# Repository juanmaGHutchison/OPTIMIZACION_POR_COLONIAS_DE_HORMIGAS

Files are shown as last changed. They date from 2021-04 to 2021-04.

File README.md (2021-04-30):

# Proyecto Final de Carrera: Diseño y Fabricación de Robots basados en Arduino para realizar el Algoritmo de Colonias de Hormigas.

_El proyecto permite realizar una ejecución real del Algoritmo de Colonias de Hormigas en un robot diseñado y fabricado en Arduino, diseño del robot disponible en el mismo proyecto._

Podemos encontrar una breve explicación además de una ejecución del robot finalizado en el siguiente enlace:
* [Ejecución ACO en Arduino](https://www.youtube.com/watch?v=iJVlAWncoFY&t=352s) - Video explicativo con posterior ejecución del Algoritmo de Colonias de Hormigas.

Y tenemos otro video en el cual se detalla el montaje de dicho robot en Arduino:
* [Montaje robot ACO](https://www.youtube.com/watch?v=88lnHN8jg98) - Video explicativo del montaje del robot en Arduino.

## Descripcion de directorios y archivos

_Descripción de los directorios y archivos disponibles en el proyecto:_

* 'ACO_CPP': En este directorio se encuentran los archivos necesarios para ejecutar el Algoritmo de Colonias de Hormigas en el lenguaje C++. De este programa se ha realizado gran parte de la experimentación del archivo 'Gomez-Hutchison-JuanManuel_TFG' Capítulo 4.
* 'ACOv2_robot': En este directorio se encuentra el proyecto final realizado en Arduino el cual se cargará físicamente al Robot.
* 'ACOv2_servidor': En este directorio se encuentra la parte del servidor, el cual se encargará, entre otras funciones de comunicar a las hormigas y actualizar las feromonas del mapa.
* 'BLUETOOTH_PRUEBA': En este directorio se encuentra un código simple para testear la comunicación Bluetooth entre el Robot y el servidor.
* 'CNYboardV2.0': Directorio donde se almacena el proyecto de diseño de la PCB al que irán conectados los sensores CNY70. Podemos encontrar la información en la documentación del archivo 'Gomez-Hutchison-JuanManuel_TFG', Sección 3.3.4.1.
* 'TEST_PIEZAS_HORMIGAS': Directorio que contiene código en Arduino para el testeo de piezas individuales del Robot, sensores, actuadores... así como de algunas pruebas de integración de éstos. 
* 'shieldV2.0.1': Directorio donde se almacena el proyecto de diseño de la PCB al que irán interconectados todos los componentes electrónicos. Podemos encontrar la información en la documentación del archivo 'Gomez-Hutchison-JuanManuel_TFG', Sección 3.3.4.2.
* 'Diseño_soporte3D': Directorio que contiene el diseño del soporte de la batería de nuestro robot.
* 'Mapa': Directorior que contiene el diseño del mapa así como las imágenes listas para imprimir.
* 'Gomez-Hutchison-JuanManuel_TFG': Archivo que contiene la documentación completa del proyecto, para cualquier tipo de duda referente al proyecto, acceder a este archivo.

### Pre-requisitos 

_Que cosas necesitas para instalar el software:_

* Arduino IDE en su última versión.
* Qt creator v4.4.10 o superior.
* Opcional: Compilador clang++ para ejecución del código en C++. Compilado con Makefile.

### Instalación 

_Simplemente tendremos que cargar el código en Arduino en el robot una vez fabricado, imprimir el mapa sobre el que se lanzará al Robot, y en un PC el código del servidor creado en Qt._

## Ejecutando las pruebas 

_Para la obtención de resultados iniciamos el servidor en Qt, lanzamos el Robot en el mapa y seguimos los pasos descritos en el documento 'Gomez-Hutchison-Juanmanuel_TFG' en la Sección 3.10_

### Analice las pruebas end-to-end 

_Los resultados de las pruebas realizadas y contrastadas a la vez que justificadas las encontramos en el documento 'Gomez-Hutchison-Juanmanuel_TFG' en el Capítulo 4_

## Construido con 

_Herramientas utilizadas para el proyecto_

* [Qt creator](https://www.qt.io/product/development-tools) - Usado para hacer el programa servidor.
* [Arduino IDE](https://www.arduino.cc/) - Usado para hacer el programa del Robot en Arduino 
* [Clang](https://clang.llvm.org/) - Usado para compilar el Programa en C++
* [GnuPlot](http://www.gnuplot.info/) - Usado para generar Gráficas
* [Eagle](https://www.autodesk.com/products/eagle/overview?plc=F360&term=1-YEAR&support=ADVANCED&quantity=1) - Usado para realizar el diseño de las PCB
* [Fusion 360](https://www.autodesk.es/products/fusion-360/overview?term=1-YEAR) - Usado para realizar el diseño 3D
* [InkScape](https://inkscape.org/es/) - Usado para el diseño del mapa
* [Latex](https://es.overleaf.com) - Usado para escribir la documentación.

## Autores 

_Ayudas ofrecidas_

* **Arturo Morgado Estévez** - *Estructuración del proyecto y electrónica*
* **Abel García Otero** - *Electrónica*
* **Ignacio Díaz Cano** - *Documentación y codificación* - [ignaciodc](https://github.com/ignaciodc)

---
Realizado por [juanmaGHutchison](https://github.com/juanmaGHutchison)

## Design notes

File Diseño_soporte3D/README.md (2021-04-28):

# Diseño del soporte 3D para la batería.

_Estructura de soporte para batería la cuál va atornillada a la parte inferior del chasis del robot._

## Descripción de archivos del directorio

_Descripción de los archivos principales de este directorio:_

* 'soporte.stl': archivo stl para futura impresión 3D.

### Pre-requisitos 

_Programa propio de la impresora para imprimir el archivo_

## Construido con 

_Herramientas utilizadas para el proyecto_

* [Fusion 360](https://www.autodesk.es/products/fusion-360/overview?term=1-YEAR) - Usado para realizar el diseño 3D

---
Realizado por [juanmaGHutchison](https://github.com/juanmaGHutchison)

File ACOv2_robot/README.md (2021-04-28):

# Algoritmo de Colonias de Hormigas: Robot en Arduino.

_Código en Arduino(C++) que simula como la hormiga busca comida, se toma parte del Algoritmo de colonias de hormigas, la decisi n de tomar el camino._

## Descripci n de archivos del directorio

_Descripción del archivo principal de este directorio. El resto de archivos podemos encontrarlos descritos en el documento 'Gomez-Hutchison-JuanManuel_TFG' en la Sección 3.5.2:_

* 'ACOv2_robot.ino': Código principal en Arduino, el cual cargaremos en el robot físicamente.

### Pre-requisitos 

_Que cosas necesitas para instalar el software:_

* Arduino IDE en su  ltima versi n.

### Instalación 

_Cargamos el código en el puerto serie al que está conectado el robot al PC._

## Ejecutando las pruebas 

_Para la ejecuci n debemos arrancar el servidor, posicionar sobre el nodo azul del mapa al robot, encenderlo, y pulsar sobre el botón 'Init pheromones' en el programa servidor._

## Construido con 

_Herramientas utilizadas para el proyecto_

* [Arduino IDE](https://www.arduino.cc/) - Usado para hacer el programa del Robot en Arduino 

---
Realizado por [juanmaGHutchison](https://github.com/juanmaGHutchison)

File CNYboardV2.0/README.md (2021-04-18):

# Diseño de Circuito Impreso para sensores CNY70.

_Proyecto realizado en Eagle donde se muestran los esquemáticos y el diseño de dicho esquemático donde se interconectan los sensores ópticos infrarrojos CNY70._

## Descripción de archivos del directorio

_Descripción de los archivos principales de este directorio:_

* 'CNYboard.brd': Diseño del circuito impreso.
* 'CNYboard.pdf': PDF donde se muestra el diseño realizado en el archivo 'CNYboard.brd'.
* 'CNYboard.sch': Esquemático del circuito impreso.
* 'CNYboard.pdf': PDF donde se muestra el esquemático realizado en el archivo 'CNYboard.sch'.
* 'eagle.epf': Archivo de tipo proyecto, el cual abrira los archivos en el programa Eagle.

### Pre-requisitos 

_Que cosas necesitas para instalar el software:_

* Autodesk Eagle en su última versión.

## Ejecutando las pruebas 

_PCB totalmente testeada tanto por software con la herramienta DRC, tanto impresa, de manera empírica._

## Construido con 

_Herramientas utilizadas para el proyecto_

* [Eagle](https://www.autodesk.com/products/eagle/overview?plc=F360&term=1-YEAR&support=ADVANCED&quantity=1) - Usado para realizar el diseño de las PCB

---
Realizado por [juanmaGHutchison](https://github.com/juanmaGHutchison)

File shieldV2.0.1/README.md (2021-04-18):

# Diseño de Circuito Impreso para la interconexión de componentes.

_Proyecto realizado en Eagle donde se muestran los esquemáticos y el diseño de dicho esquemático donde se interconectan los componentes electrónicos._

## Descripción de archivos del directorio

_Descripción de los archivos principales de este directorio:_

* 'shield.brd': Diseño del circuito impreso.
* 'shield.pdf': PDF donde se muestra el diseño realizado en el archivo 'shield.brd'.
* 'shield.sch': Esquemático del circuito impreso.
* 'shield.pdf': PDF donde se muestra el esquemático realizado en el archivo 'shield.sch'.
* 'eagle.epf': Archivo de tipo proyecto, el cual abrira los archivos en el programa Eagle.

### Pre-requisitos 

_Que cosas necesitas para instalar el software:_

* Autodesk Eagle en su última versión.

## Ejecutando las pruebas 

_PCB totalmente testeada tanto por software con la herramienta DRC, tanto impresa, de manera empírica._

## Construido con 

_Herramientas utilizadas para el proyecto_

* [Eagle](https://www.autodesk.com/products/eagle/overview?plc=F360&term=1-YEAR&support=ADVANCED&quantity=1) - Usado para realizar el diseño de las PCB

---
Realizado por [juanmaGHutchison](https://github.com/juanmaGHutchison)

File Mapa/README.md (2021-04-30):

# Diseño del mapa sobre el que se ejecutará el robot.

_Mapa que representa el grafo sobre el que el robot en Arduino realizará la ejecución. Se imprimirá dicho diseño en papel Din A3._

## Descripción de archivos del directorio

_Descripción de los archivos principales de este directorio:_

* 'mapaV4.svg': archivo para editar el mapa.
* 'mapaV4.png': foto del archivo del mapa.
* 'mapaV4.pdf': archivo pdf que contiene la foto del mapa, perfecto para imprimir.

## Construido con 

_Herramientas utilizadas para el proyecto_

* [InkScape](https://inkscape.org/es/) - Usado para el diseño del mapa

---
Realizado por [juanmaGHutchison](https://github.com/juanmaGHutchison)

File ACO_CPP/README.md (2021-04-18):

# Algoritmo de Colonias de Hormigas en C++.

_Código en C++ para la ejecución completa del Algoritmo de Colonias de Hormigas, este código es independiente del robot, se puede ejecutar para la comprobación de resultados._

## Descripción de archivos del directorio

_Descripción de los archivos disponibles en este directorio:_

* 'camino.hpp': Contiene todo lo referente a los caminos que tome la hormiga así como de crear el mapa (Grafo).
* 'hormigas.hpp': Contiene las operaciones y atributos que definen una hormiga.
* 'listaenla.hpp': Se utiliza el ##Tipo Abstracto de Datos## Lista con la implementación de nodos enlazados para guardar el recorrido que ha tomado una hormiga para así derivar posteriormente, su costo.
* 'Makefile': Script para compilar el código descrito en este directorio ejecutando el comando 'make' se generará automáticamente el archivo ejecutable. Se utiliza el compilador 'Clang++'.
* 'pt.cpp': La iniciales del archivo 'pt' significan 'prueba tablero', hace referencia al código principal de ejecución.
* 'tablero.hpp': Este archivo es el más importante ya que enlaza casi todas las clases implementadas con la principal 'pt.cpp'.

Todo lo mencionado en este apartado lo podemos encontrar en la Sección 3.2.3.

### Pre-requisitos 

_Que cosas necesitas para instalar el software:_

* Compilador clang++ para ejecución del código en C++. 
* Ejecutar el archivo 'Makefile' sobre una terminal Linux.

### Instalación 

_Posicionado con una terminal en Linux sobre este directorio ejecutamos el comando:_

```
make
```

## Ejecutando las pruebas 

_Para la ejecución del código en C++ después de completar la ##Instalación## se generará el archivo 'test-tablero' el cual será ejecutable_

```
./test-tablero
```

## Construido con 

_Herramientas utilizadas para el proyecto_

* [Clang](https://clang.llvm.org/) - Usado para compilar el Programa en C++

---
Realizado por [juanmaGHutchison](https://github.com/juanmaGHutchison)

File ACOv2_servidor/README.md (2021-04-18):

# Algoritmo de Colonias de Hormigas: Servidor del robot.

_Código en C++ referente al servidor realizado en Qt._

## Descripción de archivos del directorio

_Descripción de los archivos del proyecto servidor disponibles en el documento 'Gomez-Hutchison-JuanManuel_TFG' en la Sección 3.8.3._

### Pre-requisitos 

_Que cosas necesitas para instalar el software:_

* QtCreator v4.4.10 o superior.

### Instalación 

_Cargar el programa en el IDE del QtCreator y generar un archivo ejecutable o bien ejecutarlo desde el mismo IDE._

## Ejecutando las pruebas 

_Para la ejecución debemos arrancar el servidor, posicionar sobre el nodo azul del mapa al robot, encenderlo, y pulsar sobre el botón 'Init pheromones' en el programa servidor­._

## Construido con 

_Herramientas utilizadas para el proyecto_

* [Qt creator](https://www.qt.io/product/development-tools) - Usado para hacer el programa servidor.

---
Realizado por [juanmaGHutchison](https://github.com/juanmaGHutchison)

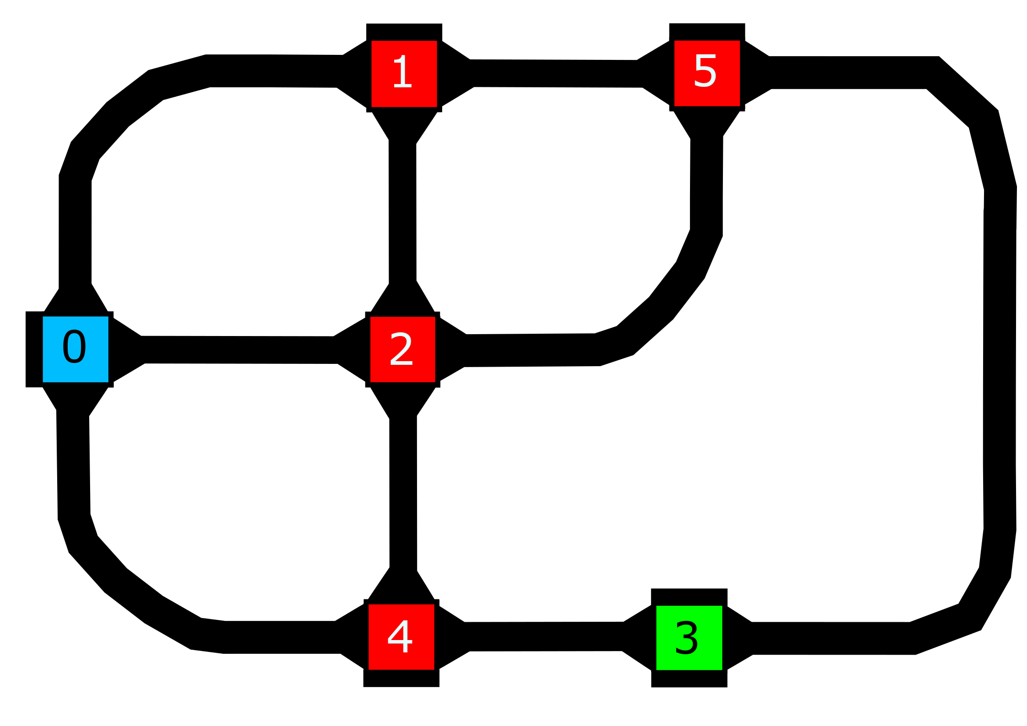
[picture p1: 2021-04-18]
ACOv2_servidor/pictures/mapa-Picture.png

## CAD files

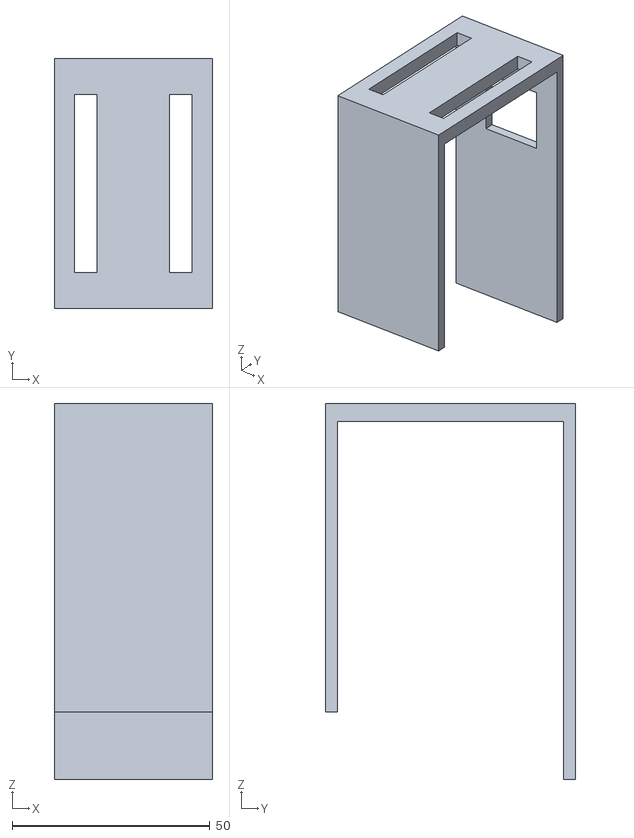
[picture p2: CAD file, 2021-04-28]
Diseño_soporte3D/soporte.stl
40.0 x 63.3 x 95.0

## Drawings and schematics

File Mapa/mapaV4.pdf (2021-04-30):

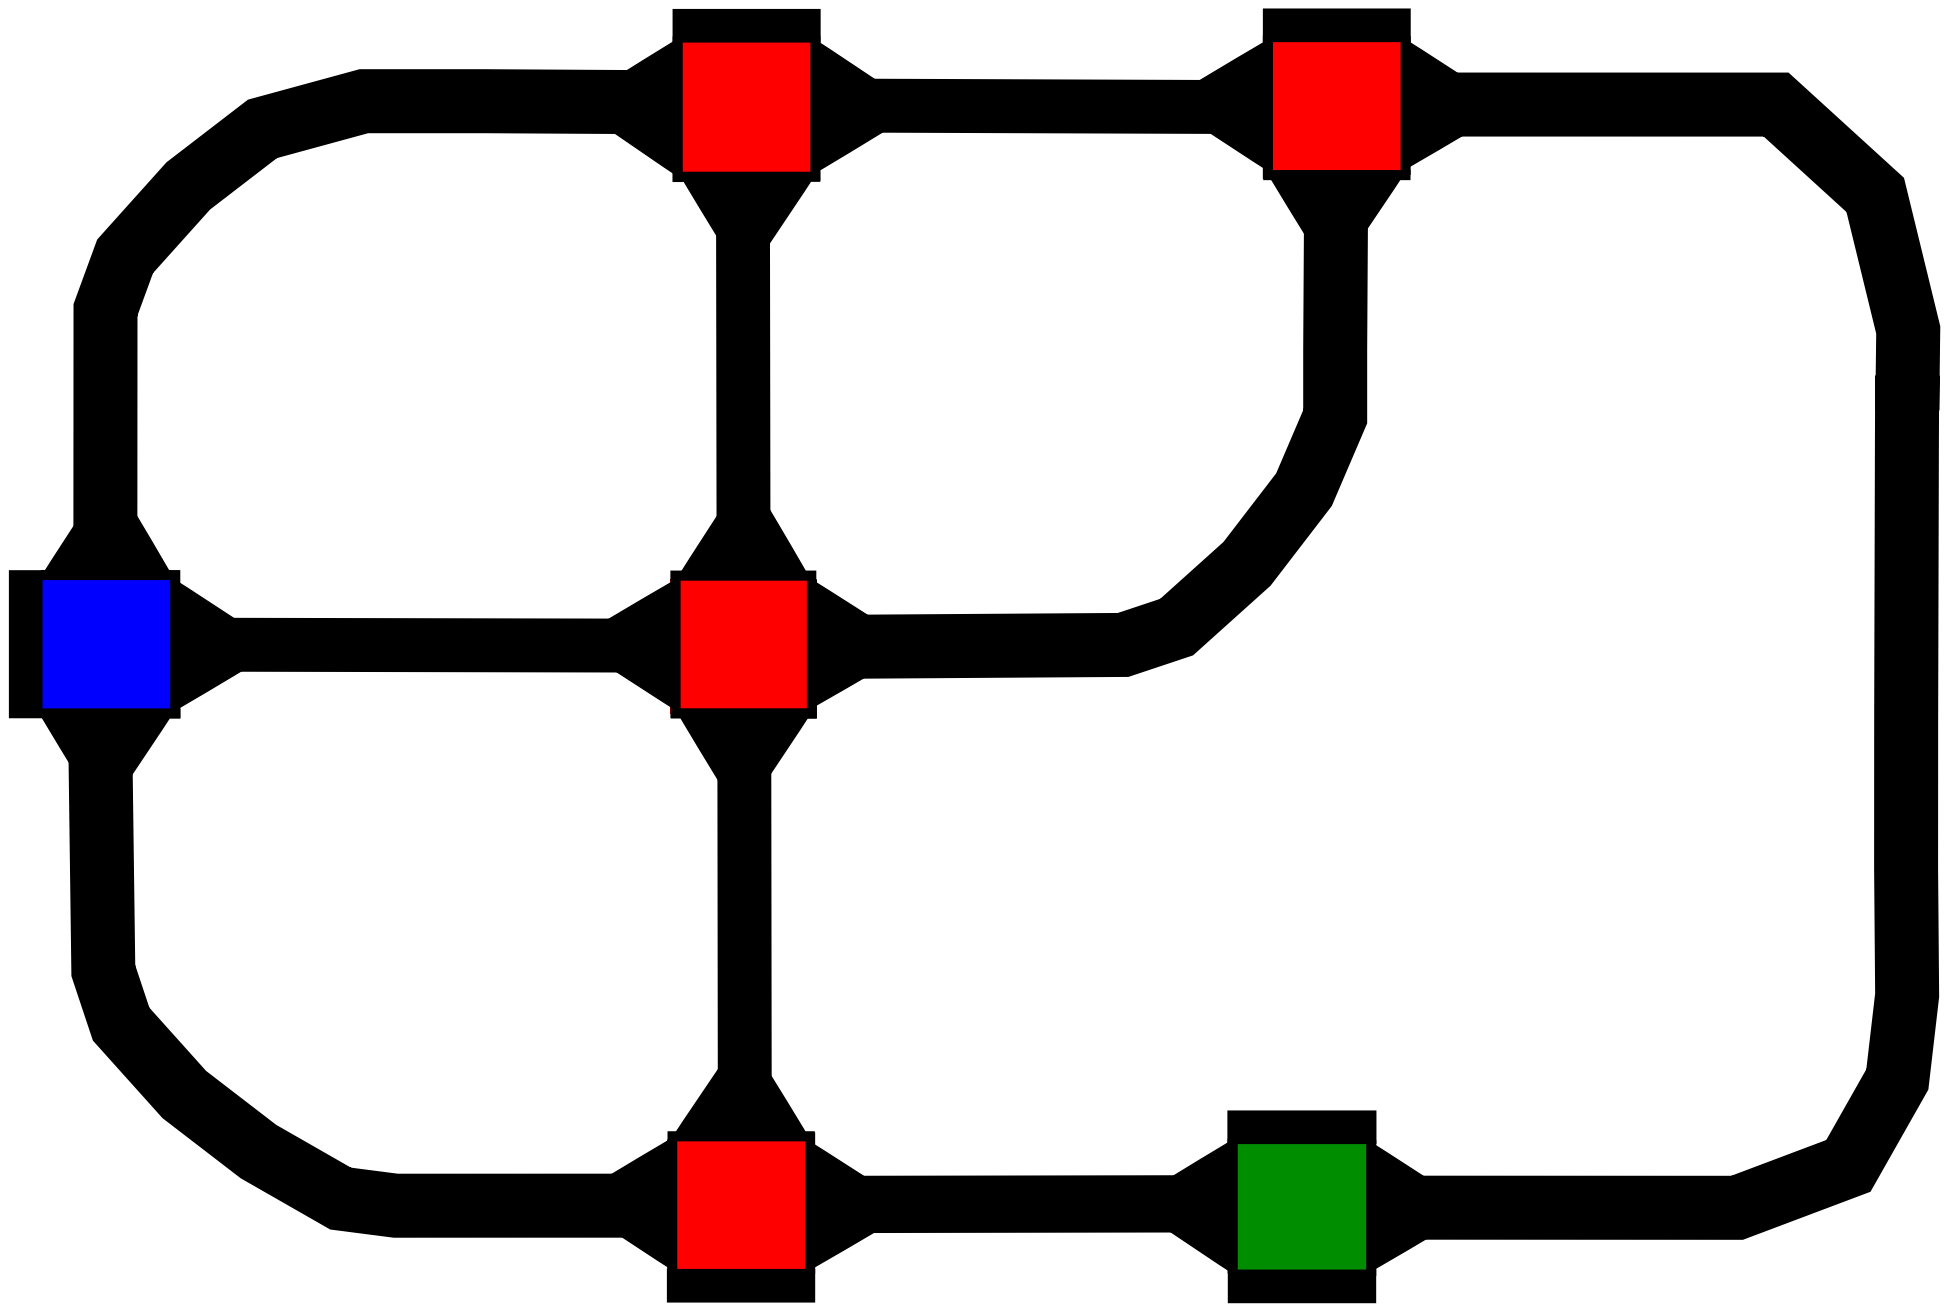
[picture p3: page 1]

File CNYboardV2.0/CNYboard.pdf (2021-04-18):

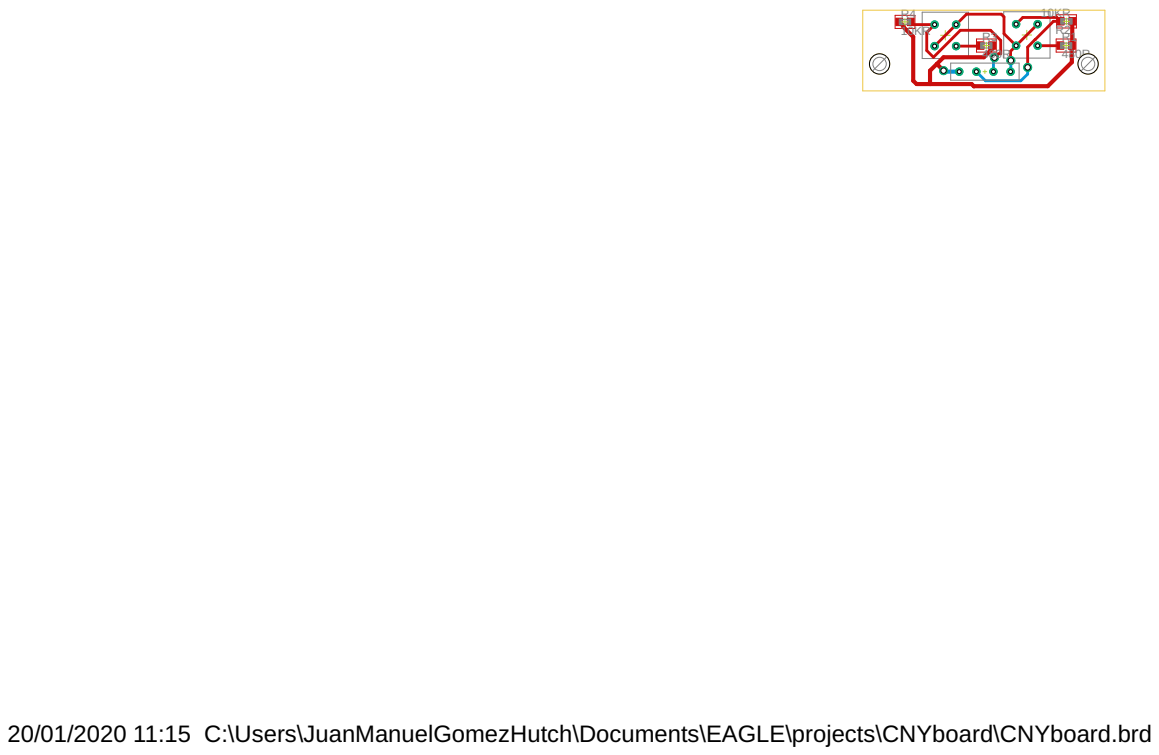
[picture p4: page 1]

20/01/2020 11:15 C:\Users\JuanManuelGomezHutch\Documents\EAGLE\projects\CNYboard\CNYboard.brd

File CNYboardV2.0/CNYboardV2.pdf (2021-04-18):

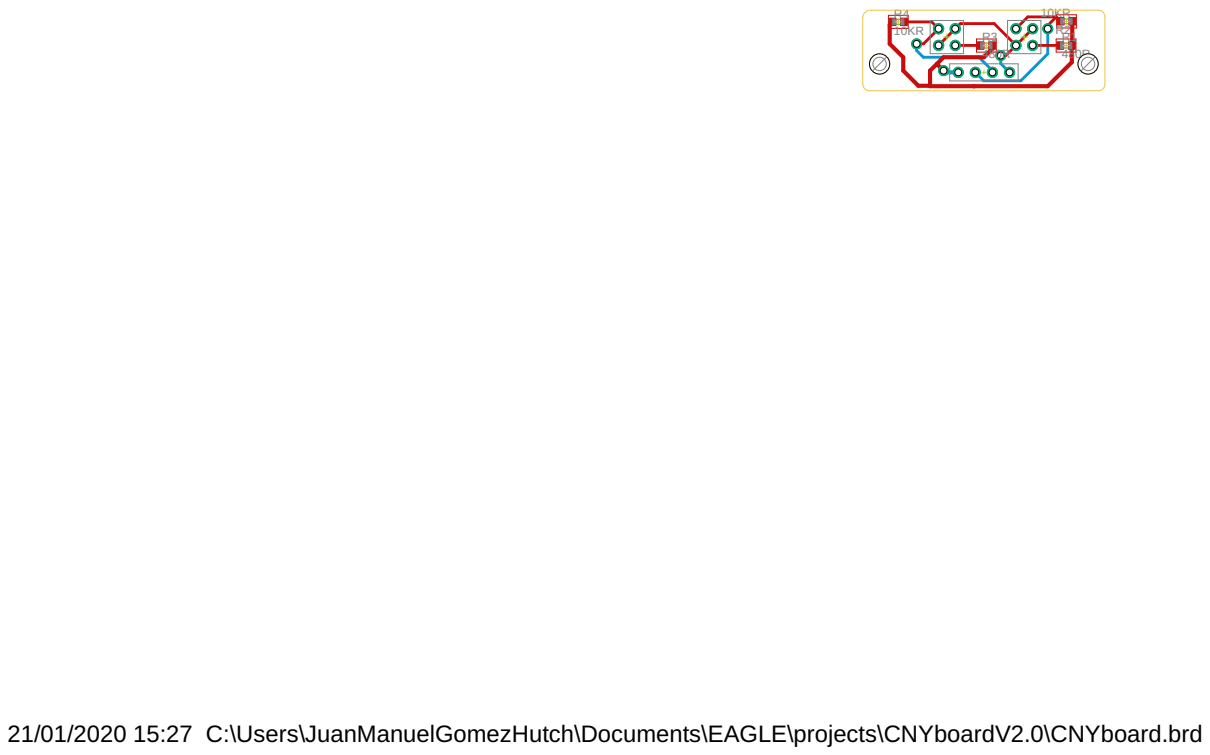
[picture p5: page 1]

21/01/2020 15:27 C:\Users\JuanManuelGomezHutch\Documents\EAGLE\projects\CNYboardV2.0\CNYboard.brd

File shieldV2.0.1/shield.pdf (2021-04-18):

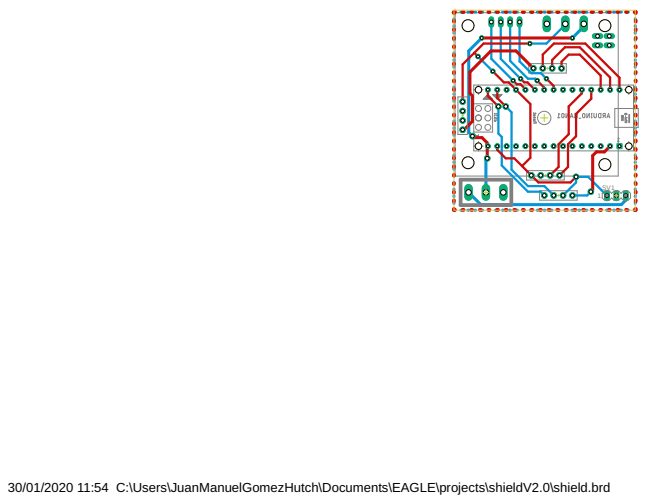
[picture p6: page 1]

30/01/2020 11:54 C:\Users\JuanManuelGomezHutch\Documents\EAGLE\projects\shieldV2.0\shield.brd

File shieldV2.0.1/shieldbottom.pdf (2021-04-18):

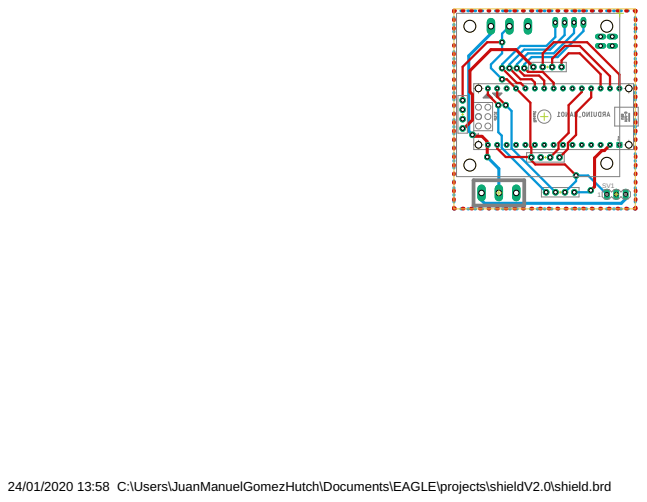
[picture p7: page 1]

24/01/2020 13:58 C:\Users\JuanManuelGomezHutch\Documents\EAGLE\projects\shieldV2.0\shield.brd

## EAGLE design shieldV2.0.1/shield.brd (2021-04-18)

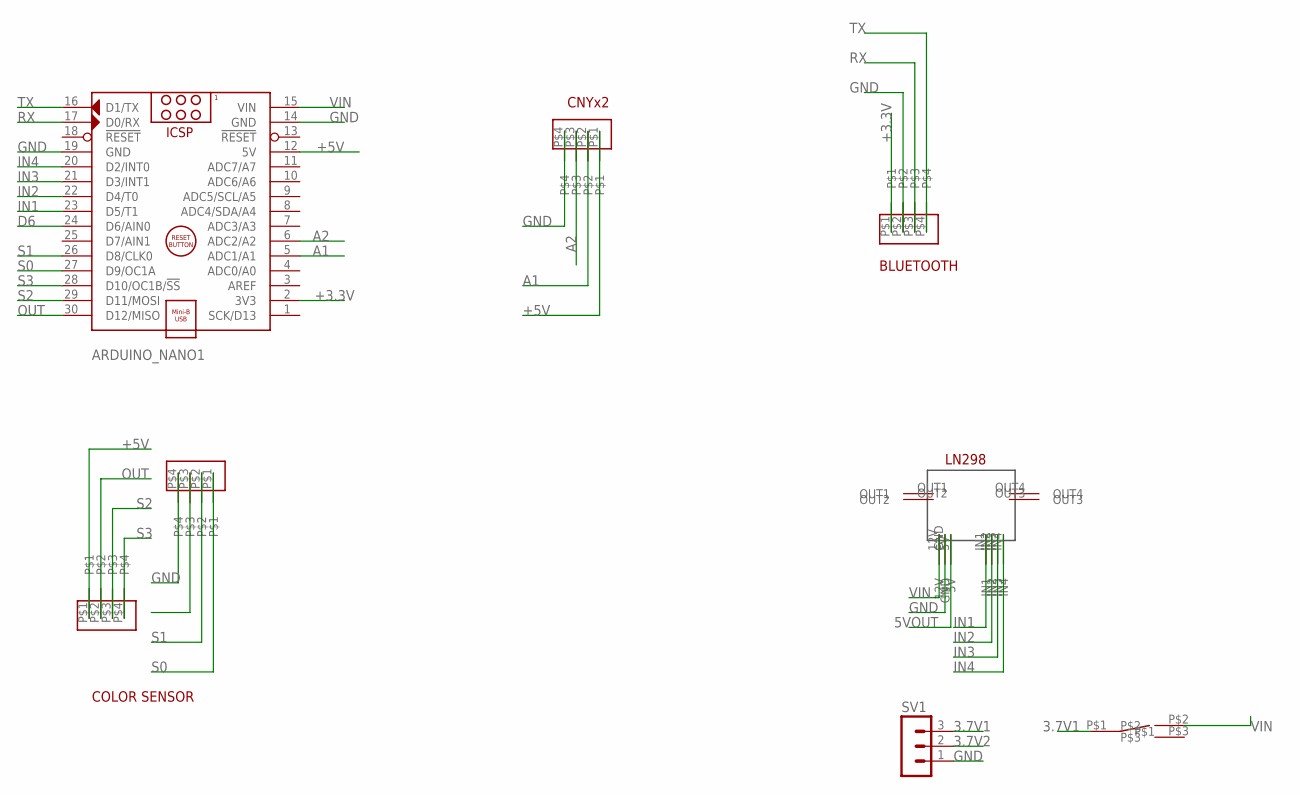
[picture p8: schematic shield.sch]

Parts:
ARDUINO_NANO1: ARDUINO_NANO
SV1: MA03-1
U$1, U$2, U$4, U$6: PIN4
U$3: INTERRUPTOR
U$5: LN298V2

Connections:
3.7V1: SV1.3, U$3.P$1
3.7V2: SV1.2
5VOUT: U$5.5V
+3.3V: ARDUINO_NANO1.2 (3V3), U$1.P$1
+5V: ARDUINO_NANO1.12 (5V), U$2.P$1, U$6.P$1
A1: ARDUINO_NANO1.5 (ADC1/A1), U$6.P$2
A2: ARDUINO_NANO1.6 (ADC2/A2), U$6.P$3
D6: ARDUINO_NANO1.24 (D6/AIN0)
GND: ARDUINO_NANO1.14 (GND), ARDUINO_NANO1.19 (GND), SV1.1, U$1.P$2, U$4.P$4, U$5.GND, U$6.P$4
IN1: ARDUINO_NANO1.23 (D5/T1), U$5.IN1
IN2: ARDUINO_NANO1.22 (D4/T0), U$5.IN2
IN3: ARDUINO_NANO1.21 (D3/INT1), U$5.IN3
IN4: ARDUINO_NANO1.20 (D2/INT0), U$5.IN4
OUT: ARDUINO_NANO1.30 (D12/MISO), U$2.P$2
RX: ARDUINO_NANO1.17 (D0/RX), U$1.P$3
S0: ARDUINO_NANO1.27 (D9/OC1A), U$4.P$1
S1: ARDUINO_NANO1.26 (D8/CLK0), U$4.P$2
S2: ARDUINO_NANO1.29 (D11/MOSI), U$2.P$3
S3: ARDUINO_NANO1.28 (D10/OC1B/!SS), U$2.P$4
TX: ARDUINO_NANO1.16 (D1/TX), U$1.P$4
VIN: ARDUINO_NANO1.15 (VIN), U$3.P$2, U$5.12V

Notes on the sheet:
BLUETOOTH
COLOR SENSOR
CNYx2

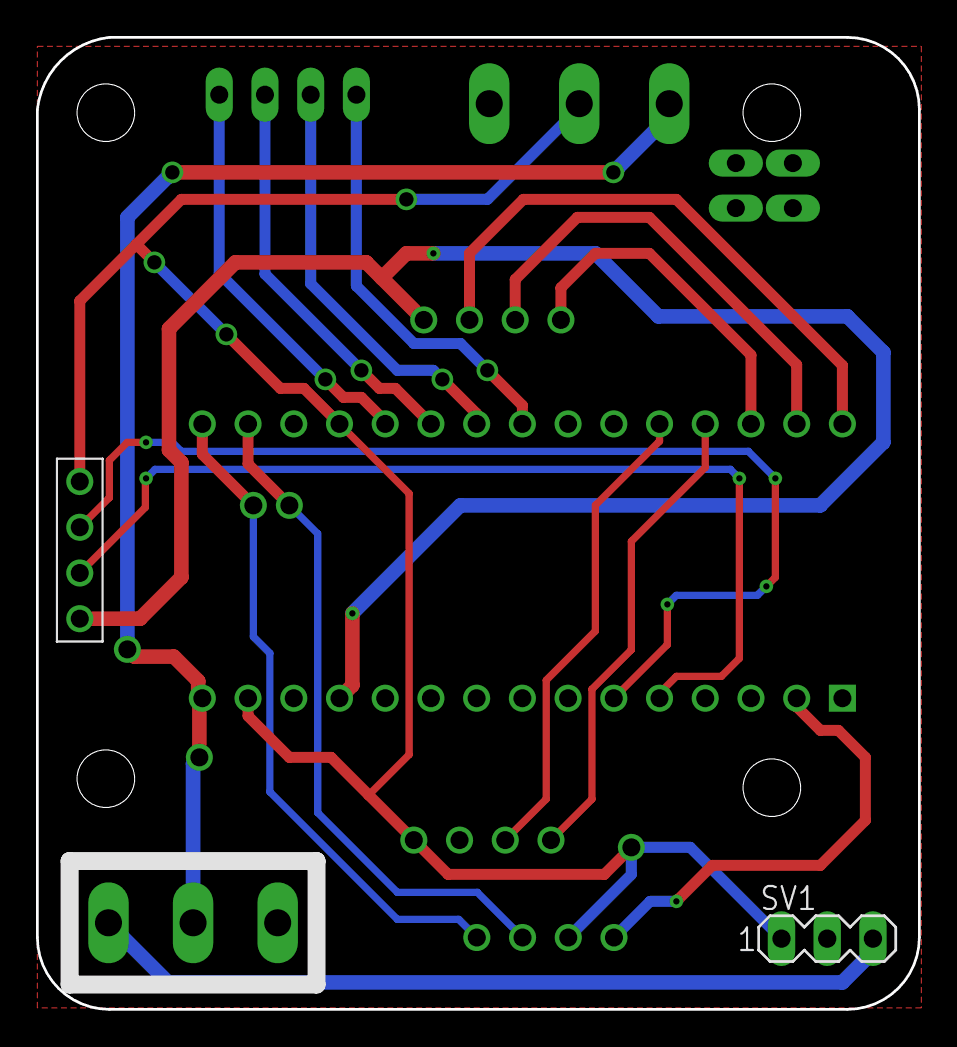
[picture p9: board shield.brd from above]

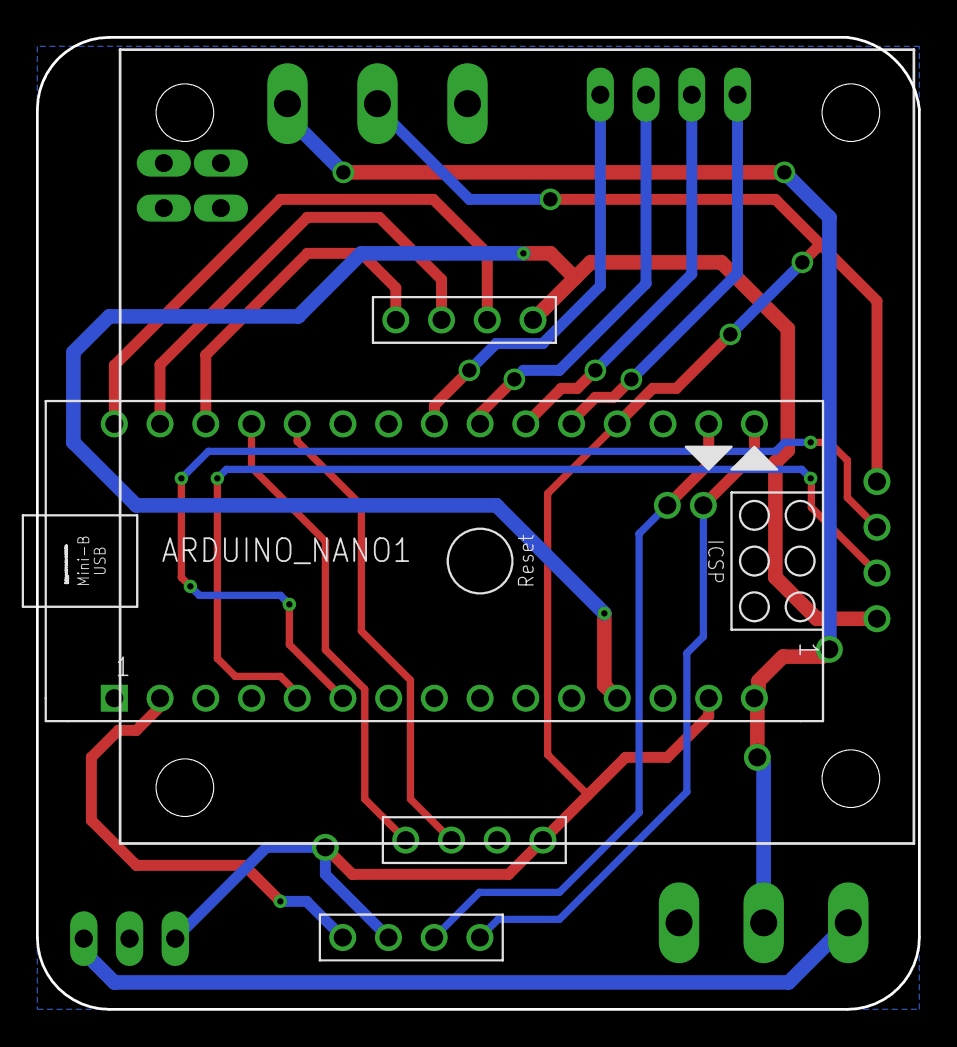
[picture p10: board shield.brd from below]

Board: 2 copper layers, 49.0 x 54.0 mm, 8 parts (5 on the bottom side), 18 nets.

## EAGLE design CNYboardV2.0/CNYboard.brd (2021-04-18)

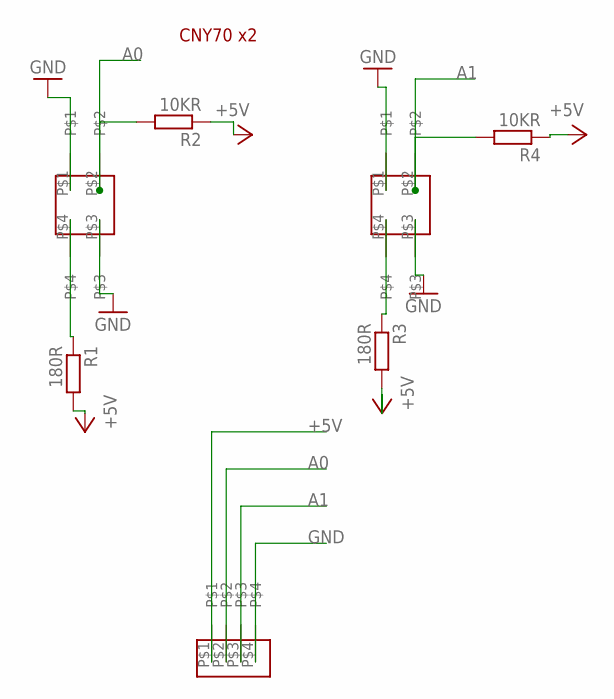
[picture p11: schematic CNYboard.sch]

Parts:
R1, R3: 180R; R0603
R2, R4: 10KR; R0603
U$1, U$2: CNYSOKET
U$3: PIN4

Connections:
+5V: R1.2, R2.1, R3.2, R4.1, U$3.P$1
A0: R2.2, U$1.P$2, U$3.P$2
A1: R4.2, U$2.P$2, U$3.P$3
GND: U$1.P$1, U$1.P$3, U$2.P$1, U$2.P$3, U$3.P$4
unnamed: R1.1, U$1.P$4
unnamed: R3.1, U$2.P$4

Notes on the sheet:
CNY70 x2

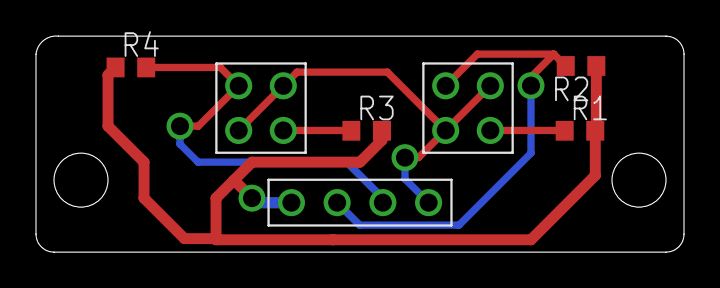
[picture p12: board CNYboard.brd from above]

Board: 2 copper layers, 36.0 x 12.0 mm, 7 parts (0 on the bottom side), 6 nets.

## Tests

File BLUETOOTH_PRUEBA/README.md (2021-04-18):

# Algoritmo de Colonias de Hormigas: Pruebas para la comunicación del Robot en Arduino.

_Código en Arduino(C++) para probar la comunicación Bluetooth del robot._

## Descripción de archivos del directorio

_Descripción del archivo principal de este directorio. El resto de archivos podemos encontrarlos descritos en el documento 'Gomez-Hutchison-JuanManuel_TFG' en la Sección 3.3.7:_

* 'BLUETOOTH_PRUEBA.ino': Código principal en Arduino, el cual cargaremos en el robot físicamente.

### Pre-requisitos 

_Que cosas necesitas para instalar el software:_

* Arduino IDE en su última versión.

### Instalación 

_Cargamos el código en el puerto serie al que esté conectado el robot al PC._

## Ejecutando las pruebas 

_Con el Módulo Bluetooth HC-05 conectado al robot, y el servidor en ejecución, cargamos el programa y realizamos una transmisión con el botón 'Start Transmission'­._

## Construido con 

_Herramientas utilizadas para el proyecto_

* [Arduino IDE](https://www.arduino.cc/) - Usado para hacer el programa del Robot en Arduino 

---
Realizado por [juanmaGHutchison](https://github.com/juanmaGHutchison)

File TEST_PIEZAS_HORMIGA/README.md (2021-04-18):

# Algoritmo de Colonias de Hormigas: Pruebas para el Robot en Arduino.

_Código en Arduino(C++) para probar los componentes electrónicos del robot tanto individualmente como algunas pruebas de integración._

## Descripción de archivos del directorio

_Descripción del archivo principal de este directorio. El resto de archivos podemos encontrarlos descritos en el documento 'Gomez-Hutchison-JuanManuel_TFG' en la Sección 3.3.7:_

* 'TEST_PIEZAS_HORMIGA.ino': Código principal en Arduino, el cual cargaremos en el robot físicamente.

### Pre-requisitos 

_Que cosas necesitas para instalar el software:_

* Arduino IDE en su última versión.

### Instalación 

_Cargamos el código en el puerto serie al que esté conectado el robot al PC._

## Ejecutando las pruebas 

_Para probar las piezas, una vez montado el robot iremos descomentando las directivas de preprocesador escritas al principio del programa, y subiremos el código. Cada una de estas directivas vienen descritas._

## Construido con 

_Herramientas utilizadas para el proyecto_

* [Arduino IDE](https://www.arduino.cc/) - Usado para hacer el programa del Robot en Arduino 

---
Realizado por [juanmaGHutchison](https://github.com/juanmaGHutchison)

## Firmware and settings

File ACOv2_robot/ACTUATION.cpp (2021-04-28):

#include "ACTUATION.hpp"
Actuation::Actuation(): 
  cny_left_(CNY_LEFT, 870),
  cny_right_(CNY_RIGHT, 870),
  cnys_(cny_left_, cny_right_),
  previous_grade_(0)
  {}
  void Actuation::Response(uint8_t grades, uint8_t correction, bool& toogle) {
    if(toogle) {
      //Serial.println("TOOGLE ROBOT");
      motor_.roll_grades(180);
      toogle = false; 
    }
    /*Serial.print("INPUT GRADES: ");
    Serial.println(grades);*/
    previous_grade_ = to_grades(grades);
    /*Serial.print("GRADES CONVERTED: ");
    Serial.println(previous_grade_);*/
    motor_.roll_grades(previous_grade_);
    if(cnys_.bothWhite()) {
      while(!cnys_.bothBlack()) {
      if(cnys_.leftBlack())
        while(!cnys_.bothBlack() && !cnys_.bothWhite())
          motor_.right(); 
      if(cnys_.rightBlack())
        while(!cnys_.bothBlack() && !cnys_.bothWhite())
          motor_.left();
      while(cnys_.bothWhite()) 
        motor_.straight();
      }
    }  
    while(!cnys_.bothWhite()){
      if(cnys_.leftWhite())
        while(!cnys_.bothBlack() && !cnys_.bothWhite())
          motor_.right();
      if(cnys_.rightWhite())
        while(!cnys_.bothBlack() && !cnys_.bothWhite())
          motor_.left();
       while(cnys_.bothBlack()) 
          motor_.straight();
    }
    motor_.botStop();
    delay(2000);
    while(!cnys_.bothBlack()) {
      if(cnys_.leftBlack())
        while(!cnys_.bothBlack() && !cnys_.bothWhite())
          motor_.right(); 
      if(cnys_.rightBlack())
        while(!cnys_.bothBlack() && !cnys_.bothWhite())
          motor_.left();
      while(cnys_.bothWhite()) 
        motor_.straight();
    }
    motor_.botStop();
    delay(2000);
    /*Serial.print("INPUT CORRECTION: ");
    Serial.println(correction);*/
    motor_.roll_grades(to_grades(correction));
  }
  int Actuation::to_grades(uint8_t matrix_grades) const {
    int grades_to_roll = 0;
    switch(matrix_grades) {
        case 0:
          grades_to_roll = 0;
        break;
        case 1:
          grades_to_roll = 90;
        break;
        case 2:
          grades_to_roll = 180;
        break;
        case 3:
          grades_to_roll = 270;
        break;
      }
      return grades_to_roll;
  }
    void Actuation::straighten() {
      /*int grades_to_roll;
  
      switch(previous_grade_) {
        case 90:
          grades_to_roll = 270;
        break;
        case 270:
          grades_to_roll = 90;
        break;
        default:
          grades_to_roll = previous_grade_;
        break;
      }
      Serial.print("GRADES TO ROLL TO STRAIGHT BOT: ");
      Serial.println(grades_to_roll);
      motor_.roll_grades(grades_to_roll);
     */   
    }
    String Actuation::previous_grade() const {
      return String(previous_grade_);
    } 

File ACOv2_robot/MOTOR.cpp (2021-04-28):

#include "MOTOR.hpp"
MOTOR::MOTOR(): 
  IN1_(LN298_IN1), 
  IN2_(LN298_IN2), 
  IN3_(LN298_IN3), 
  IN4_(LN298_IN4)
  {
    pinMode(IN1_, INPUT);
    pinMode(IN2_, INPUT);
    pinMode(IN3_, INPUT);
    pinMode(IN4_, INPUT);  
    digitalWrite(IN1_, LOW);
    digitalWrite(IN2_, LOW);
    digitalWrite(IN3_, LOW);
    digitalWrite(IN4_, LOW);
  }
void MOTOR::straight() {
  digitalWrite(IN1_, HIGH);
  digitalWrite(IN2_, LOW);
  digitalWrite(IN3_, HIGH);
  digitalWrite(IN4_, LOW);
}
void MOTOR::left() {
  digitalWrite(IN1_, LOW);
  digitalWrite(IN2_, LOW);
  digitalWrite(IN3_, HIGH);
  digitalWrite(IN4_, LOW);
}
void MOTOR::right() {
  digitalWrite(IN1_, HIGH);
  digitalWrite(IN2_, LOW);
  digitalWrite(IN3_, LOW);
  digitalWrite(IN4_, LOW);
}
void MOTOR::back(){
  digitalWrite(IN1_, LOW);
  digitalWrite(IN2_, HIGH);
  digitalWrite(IN3_, LOW);
  digitalWrite(IN4_, HIGH);
}
void MOTOR::crossLeft(){
  digitalWrite(IN1_, LOW);
  digitalWrite(IN2_, LOW);
  digitalWrite(IN3_, HIGH);
  digitalWrite(IN4_, LOW);
  digitalWrite(IN1_, LOW);
  digitalWrite(IN2_, HIGH);
  digitalWrite(IN3_, HIGH);
  digitalWrite(IN4_, LOW);
}
void MOTOR::crossRight() {
  digitalWrite(IN1_, HIGH);
  digitalWrite(IN2_, LOW);
  digitalWrite(IN3_, LOW);
  digitalWrite(IN4_, LOW);  
  digitalWrite(IN1_, HIGH);
  digitalWrite(IN2_, LOW);
  digitalWrite(IN3_, HIGH);
  digitalWrite(IN4_, LOW);
}
void MOTOR::backLeft() {
  digitalWrite(IN1_, LOW);
  digitalWrite(IN2_, HIGH);
  digitalWrite(IN3_, HIGH);
  digitalWrite(IN4_, LOW);
}
void MOTOR::backRight() {
  digitalWrite(IN1_, HIGH);
  digitalWrite(IN2_, LOW);
  digitalWrite(IN3_, LOW);
  digitalWrite(IN4_, HIGH);
}
void MOTOR::turnBack(){
  digitalWrite(IN1_, HIGH);
  digitalWrite(IN2_, LOW);
  digitalWrite(IN3_, LOW);
  digitalWrite(IN4_, HIGH);
}
void MOTOR::botStop(){
  digitalWrite(IN1_, LOW);
  digitalWrite(IN2_, LOW);
  digitalWrite(IN3_, LOW);
  digitalWrite(IN4_, LOW);
}
void MOTOR::roll_grades(int grades){
  switch(grades){
    case 90:
      left();
      backLeft();
      delay(1170);
      //delay(360); //ATOMICA
      //delay(1400); //BATERIA GRANDE
      botStop();
    break;   
    case 180:
      right();
      backRight();
      delay(2500);
      //delay(730); //ATOMICA
      //delay(2688);  //BATERIA GRANDE
      botStop();
    break;    
    case 270:
      right();
      backRight();
      delay(1200);
      //delay(360); //ATOMICA
      //delay(1400);  //BATERIA GRANDE
      botStop();
    break;
  }
}

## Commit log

2021-04-18 first commit, and stable version
    [CNYboard.brd, CNYboard.sch, shield.brd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]
2021-04-28 Diseño 3D y actualización de pines
    [soporte.stl]
